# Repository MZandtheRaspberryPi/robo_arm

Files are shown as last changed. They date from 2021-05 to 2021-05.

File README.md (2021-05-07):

# robo_arm
This is a robot arm project that has two capabilities. The first is an arduino based arm that can be controlled via onboard joysticks and displays output to an OLED screen as it moves in x, y, z space with an inverse kinematic model. The second is a ROS Powered version that uses rosserial to communicate with the master node, and allows publishing of messages on a topic to command the arm in x, y, z coordinates.  
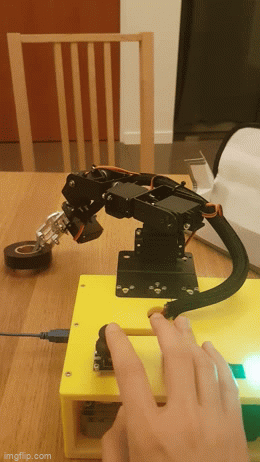
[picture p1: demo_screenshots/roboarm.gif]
roboarm
  

[Here](https://www.youtube.com/watch?v=9vvvBXWQKJA) is a demo of the arduino based version of the arm, and [here](https://www.youtube.com/watch?v=Fptv3H4Jj54) is a demo of the ros based version of the arm.  

The Arduino code for the ROS implementation is in the arduino_ros_arm folder, whereas the Arduino code for the standalone version is in the robo_arm_arduino_inverse_kinematics folder.

# Using the ROS Implementation
Follow the Steps in the Setting Up your Arm (ROS) section, and then launch the node:   
```
roslaunch robo_arm robo_arm.launch 
```  

And from here you can publish messages to control the arm:  
```
rostopic pub /robo_arm_teleop/arm_movement robo_arm/arm_control -1 '{x: 0, y: 180, z: 158, grip: 1700, duration: 1000}'
```  

# Table of Contents
[Project Phases](#Project-Phases)  
[Inverse Kinematics](#Inverse-Kinematics)  
[Setting Up your Arm (ROS)](#Setting-It-Up-ROS)  
[Setting Up your Arm (Arduino)](#Setting-It-Up-Arduino)   

# Project Phases
1. Repairing Arm
2. Testing Electronics
3. Initial Arduino Approach
4. 3d Modelling
5. Printing the Base
6. Assembly
7. Complex Arduino Software with IK Model
8. Complex ROS Software with IK Model

## Repairing the Arm
I actually got the raw parts for this arm from a friend, but it wasn't in working order when I got it, and didn't have any software.  It was too top heavy and the bottom servos couldn't support the weight well, and a lot of the joints weren't well secured. Also, the bottom piece of the arm had screws going into the plastic of the servo, so it couldn't rotate the arm left to right.    
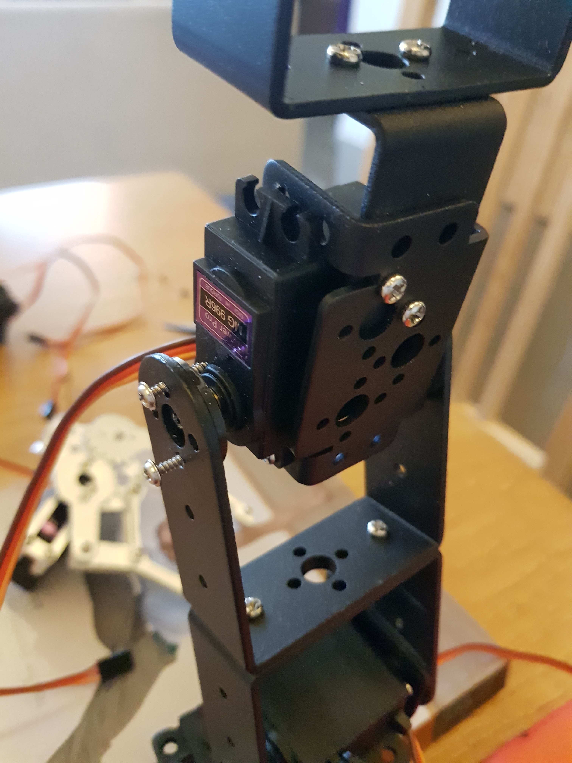
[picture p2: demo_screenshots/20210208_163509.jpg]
screws
   

I ended up replacing the servo horns with metal ones, that had screw holes that matched the screw holes of the metal body (M3). This helped me tighten the joints more securely, and not use long screws that could prevent rotation. I also removed a joint from the arm, bringing it from 6 to 5 joints to help it be not so top heavy.  

## Testing Electronics
From here, I rebuilt the arm and started testing the electronics system I wanted to put in place--powering the servos from Lipo Batteries through a 5v converter that can do up to 10 Amps.  
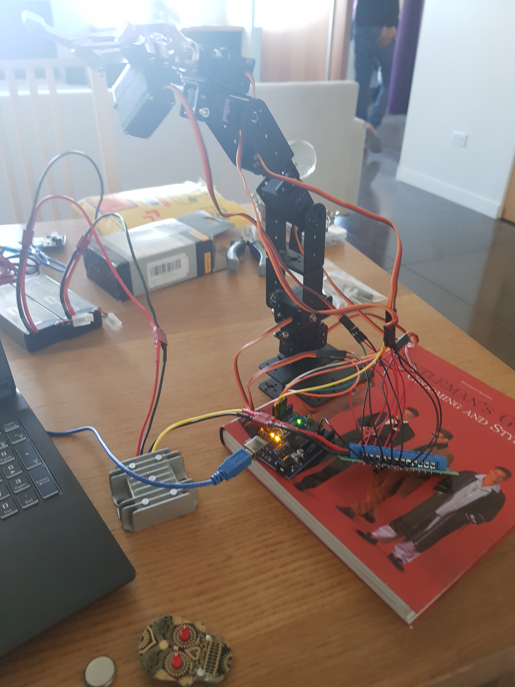
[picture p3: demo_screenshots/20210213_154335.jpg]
electronics
  

You can see here all the guts of the system with the emergency off switch, relay, OLED display, and more:  
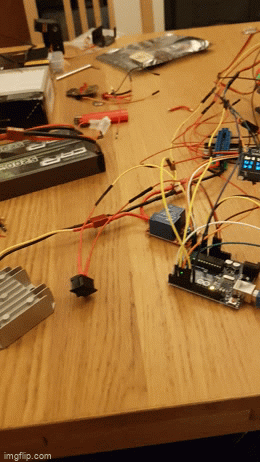
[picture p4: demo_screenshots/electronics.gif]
!electronics2
  

## Initial Arduino Approach
This would end up being simplistic code that moved each servo in angle space, moving them all in small steps to simulate coordinated motion. The Arduino code for this is in the robo_arm_arduino folder. It was an early prototype that I would build on in later software iterations, but it did serve as a proof of concept that coordinated movement was possible with the hardware setup. That said, if you wanted to move the gripper forward, you had to blend the angles yourself. Obviously this isn't ideal.  
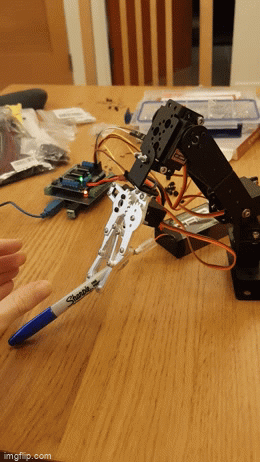
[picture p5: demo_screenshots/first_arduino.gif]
first_move
  

## 3d Modelling 
From here I wanted to tidy up the electronics, so I modelled a suitable base station. I first drew some sketches, picturing a base with electronics and the robo arm sitting on top.  
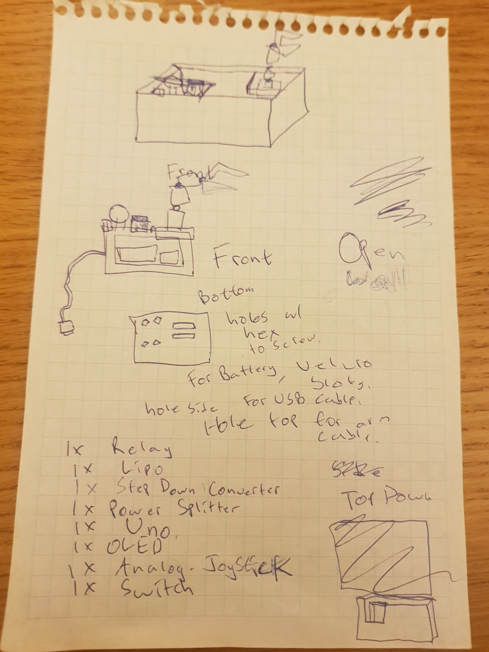
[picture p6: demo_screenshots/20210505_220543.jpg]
plan_for_model
  

And from here I modelled it in Fusion 360.
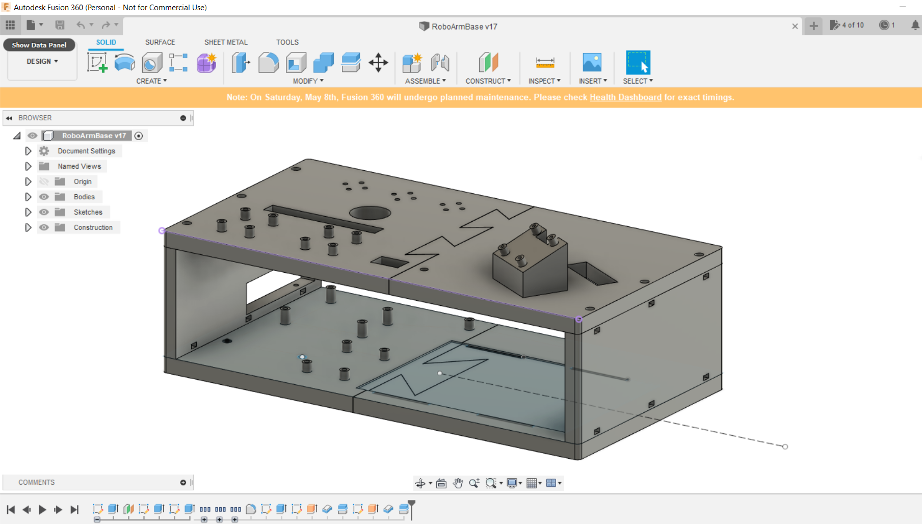
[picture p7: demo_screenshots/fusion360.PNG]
fusion360
  

Given this base was going to be quite big, 300mm by 155mm and 90mm tall, if I messed up any of the mounts or parts, it would take a lot to reprint it. So, I did a lot of prototyping for every single mounting point, as well as the mechanism that the sides of the base join to each other.  
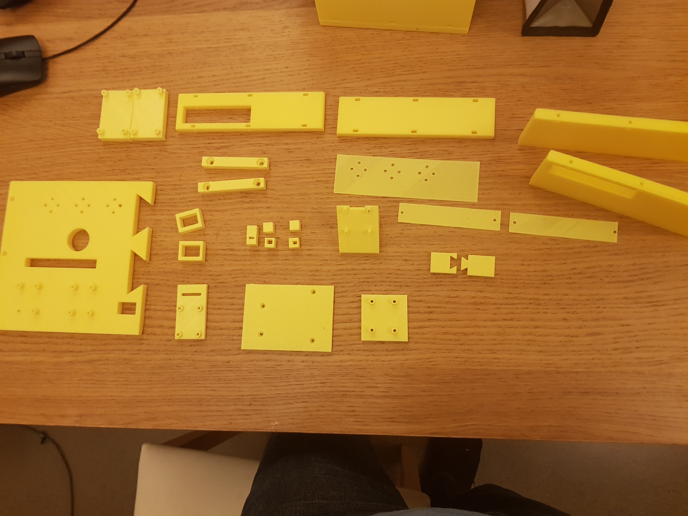
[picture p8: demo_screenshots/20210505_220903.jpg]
prototypes
  

## Printing the Base
I actually had some long put off maintenance that I had to do on my 3d printer. I put it off even longer, and kept having trouble getting prints to finish. For instance, look what I came home to one day:  
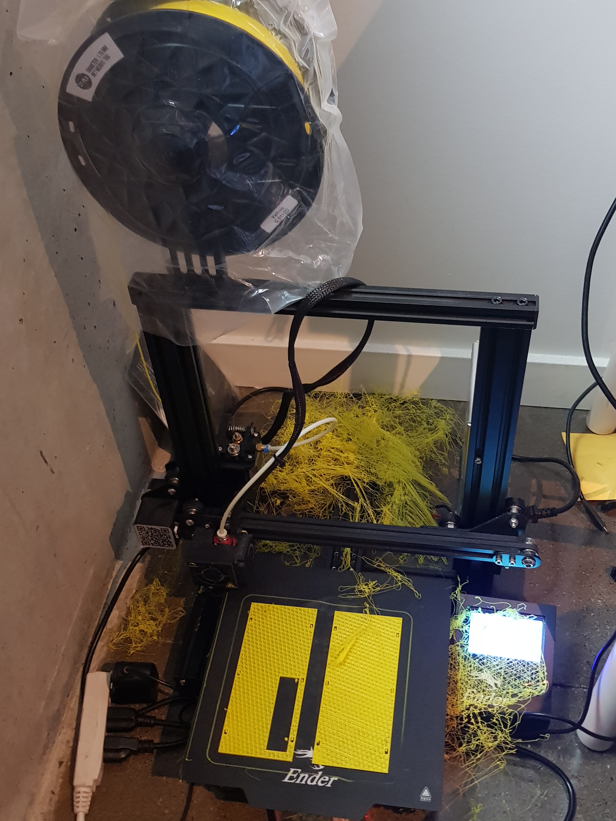
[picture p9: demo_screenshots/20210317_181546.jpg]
spaghetti
  

I eventually would install OctoPrint during this phase so that I could remotely monitor and shutdown my printer. I also replaced a clogged nozzle, replaced the springs on the 3d Printer Bed with stronger ones, and many other changes. Check out how gunked the nozzle was after one of the print failures:  
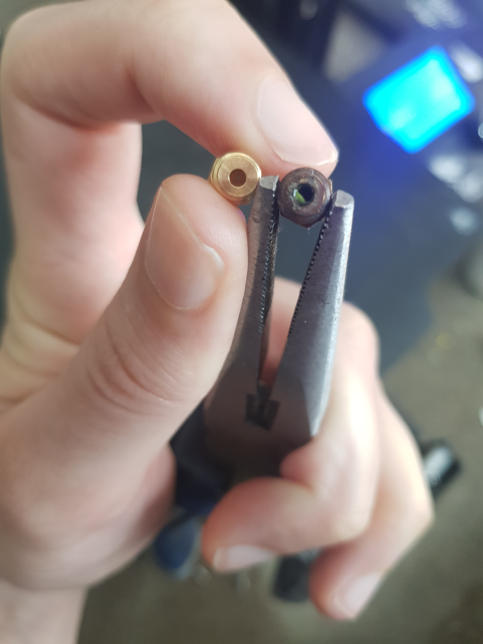
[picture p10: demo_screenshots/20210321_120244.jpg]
gunk
  

I also cleaned out the tube that feeds plastic to the extruder. you can see there was plastic stuck in it, which meant the extruder couldn't push the new plastic through:
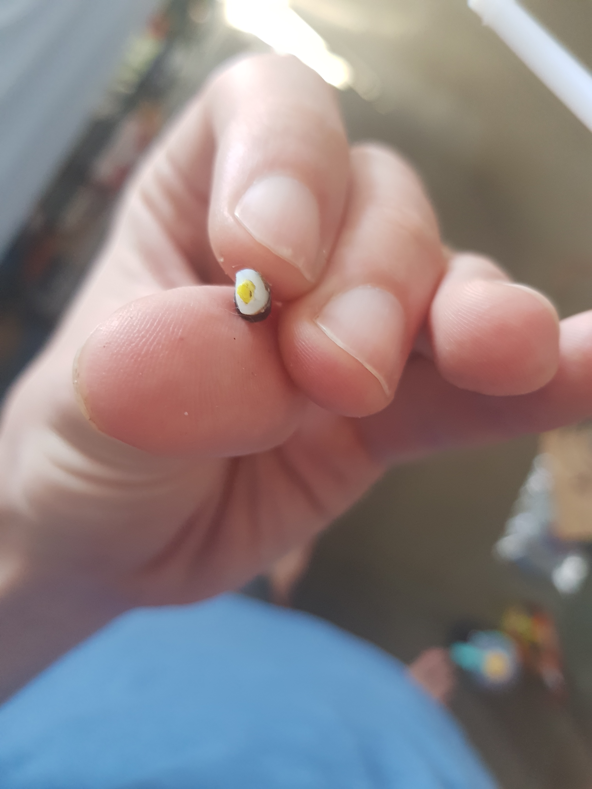
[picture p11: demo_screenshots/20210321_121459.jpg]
jam
  

This lead to problems where parts would be missing a layer, where the extruder got stuck and couldn't push plastic through:  
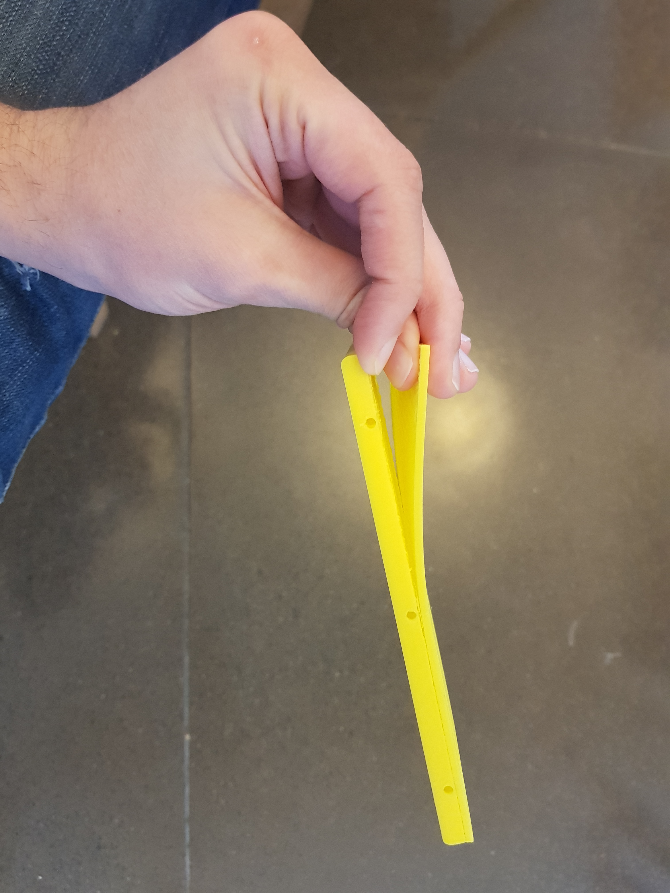
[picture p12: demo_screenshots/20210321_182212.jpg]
bad_ladyer
  

I also had an awkward problem, where when splitting up the top of the piece to print it in two seperate pieces (it was too big for my printer) I made a dovetail joint. That said, I split them using a 2mm surface instead of a .2mm surface and they couldn't fit back together again. Thankfully I only had to print one of these again as the surface extruded only into one side: 
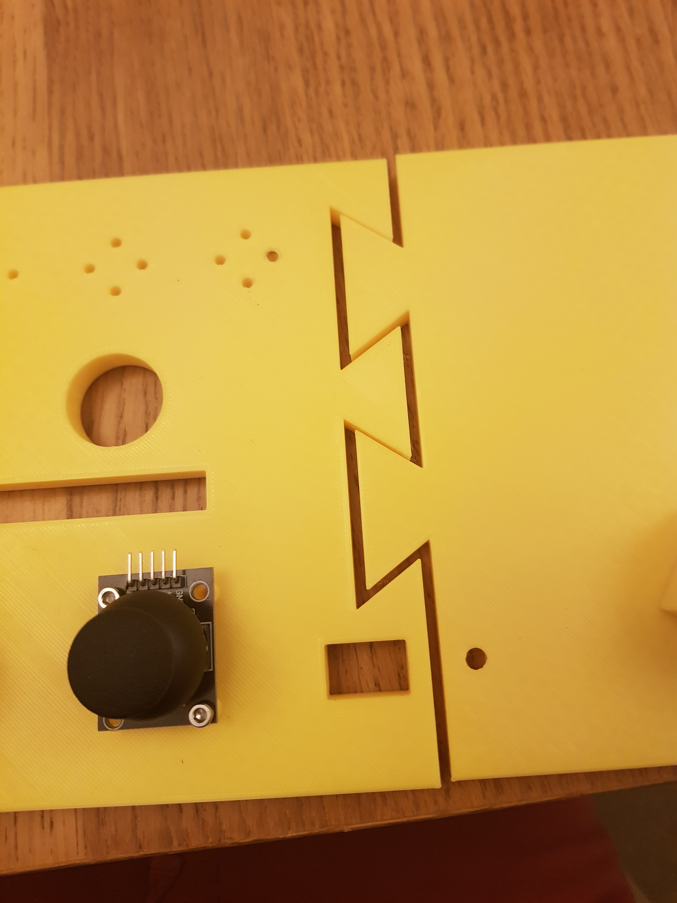
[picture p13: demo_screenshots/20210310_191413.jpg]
bad_extrude
  

I exited this phase having learned a lot about troubleshooting my printer, and having replaced a lot of parts to make the printer more durable and reliable in the future. Overall, a big win as I rely on this printer for many projects.  

## Assembly
Now I had my base and I started to assemble it with the electronics. You can see a sneak peek at everything and how it mounts. I still need to tidy up my wiring. In retrospect I could have designed wire channels into the base to help keep stuff tidy:  
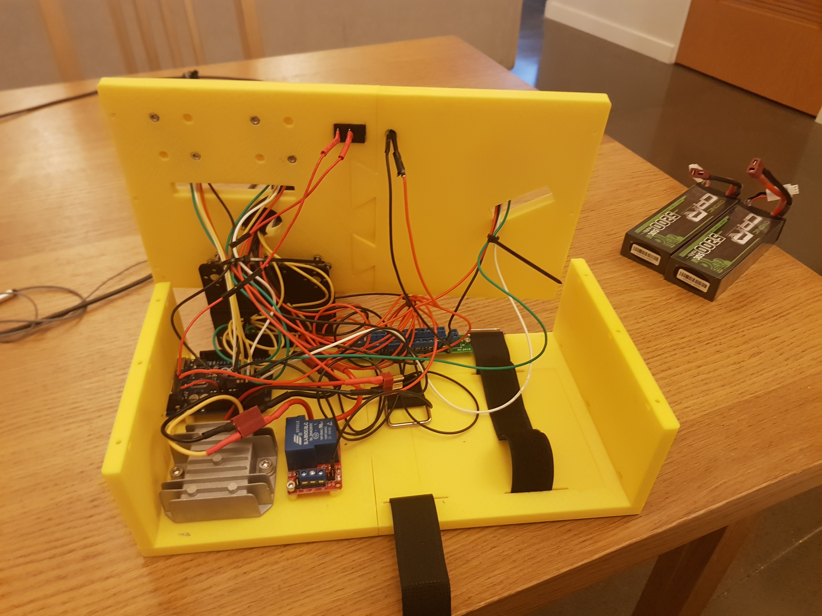
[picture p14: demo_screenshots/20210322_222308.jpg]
assembly
  

But from the top, it looks tidy:  
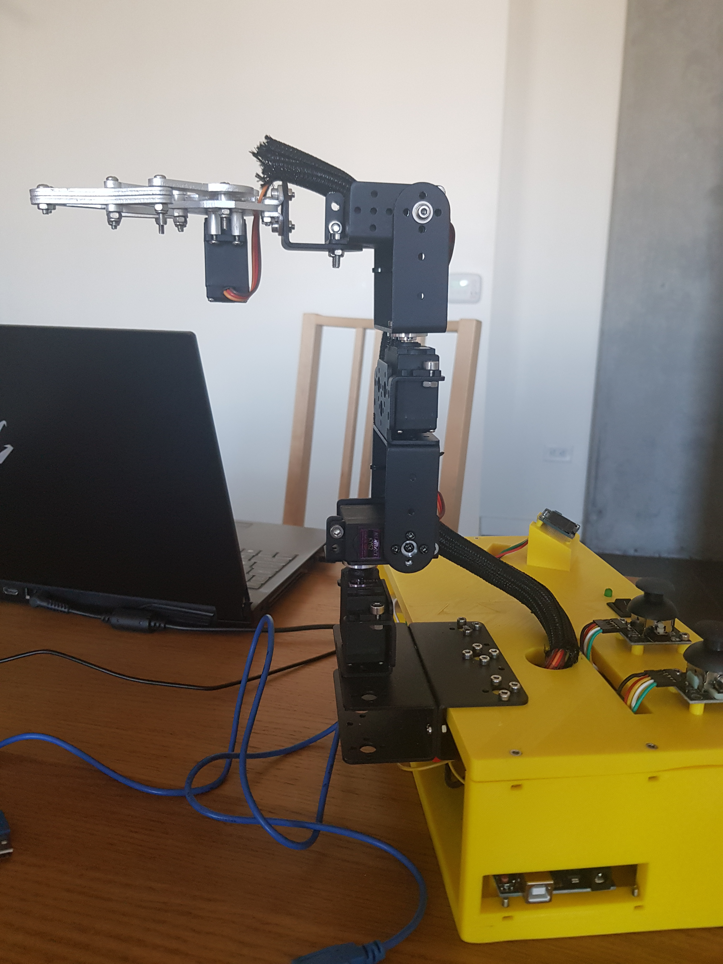
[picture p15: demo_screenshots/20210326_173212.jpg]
tidy
  

I did have a bit of a batery fiasco here where I left two batteries connected in serial for a couple nights. This lead to them overdischarging to probably about 2.5 volts, which is pretty bad. I ended up recharging them at a very low amperage, but these batteries are no longer safe to use or to charge, so I'm monitoring them carefully and will replace them soon.  

## Complex Arduino Software with IK Model
I ended up writing an IK model for the robot arm using some videos I saw from youtube and building on them to suit my robot. [This](https://www.youtube.com/watch?v=IN8tjTk8ExI)  video from James Bruton was very helpful. That said I had to make many changes for my IK model and develop some new functionality because my robot arm had different lengths for the upper and lower arm and because I added a third degree of freedom to my IK model as I wanted to control 3 servos, not 2. I'll talk about the kinematics after the project phases. That said, this software is available in the robo_arm_arduino_inverse_kinematics folder.  

## Complex ROS Software with IK Model
I started out writing pretty elaborate code to integrate the arm with ROS. I published a message with the joystick values from the robot, then on my laptop would publish a cmd_vel and a gripper control message off of that, but then when I started subscribing to those messages from the Arduino, I quickly ran out of space on the Arduino. The code for this is in the: ros_robo_arm_joy folder, and the ros code in the src folder as joy_listener.cpp. In my experience, one subscriber was already coming up close to the memory limits for the arduino, so I wanted to keep things simple. I settled on publishing a message from my laptop that had the x, y, z, gripper target, and how long to take to move there. From there the Arduino subscribed to that message and calculated the IKs to move the servos itself. The Arduino code for this approach that I settled on is in the arduino_ros_arm folder.

# Inverse Kinematics  
The IK model for this is pretty interesting. We take the point we command (x,y,z) as the point the gripper's jaws close on. Taking two dimensions, Z, X, we can solve for the arm length, and then use that to solve for various angles because we know all three sides of the ensueing triangle: 
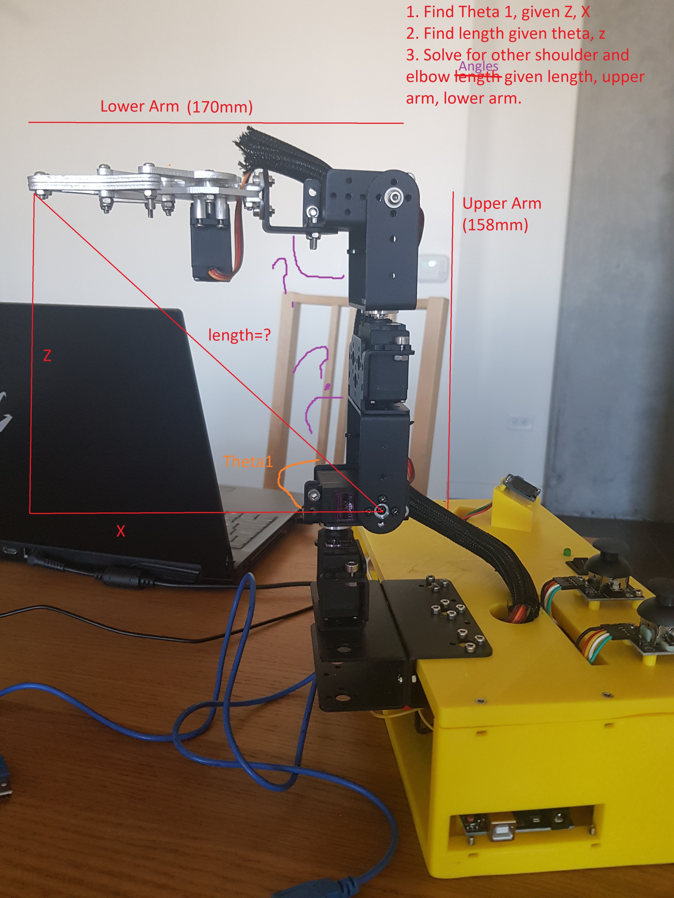
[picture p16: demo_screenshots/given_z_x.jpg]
ik
  

When we add in the third servo, the base servo of the arm, things get a tad more complicated.  

Consider this picture as if you were looking down at the robot arm and the base. Given x,y coordinates of the gripper, we can solve for the base servo angle of rotation. We can also solve for the length F that I've labeled that will be important in solving the rest of the angles.    
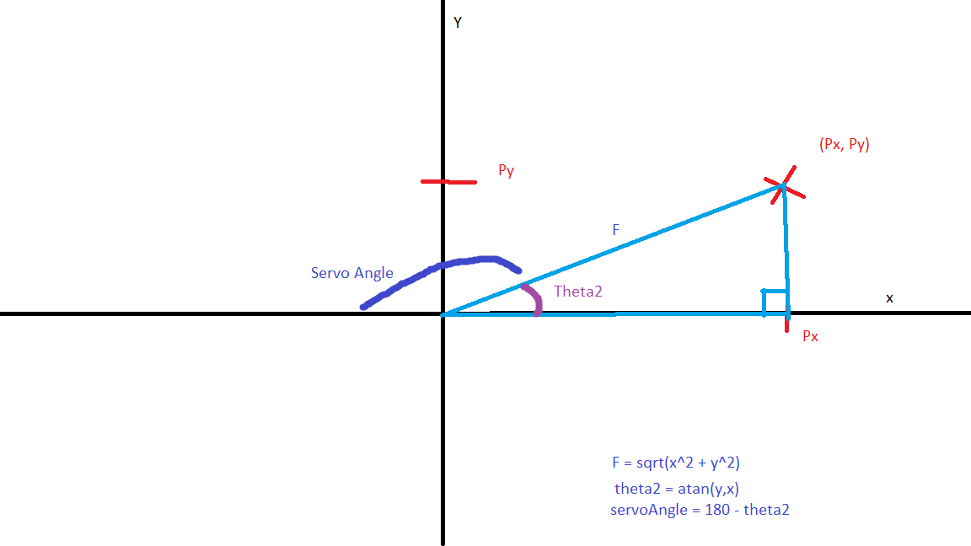
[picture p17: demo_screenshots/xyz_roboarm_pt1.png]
looking_down
  

Then in 3d space, we see F is the base of a triangle. We know the z coordinate, so can solve the third side of the triangle given its a right triangle. Now we have three sides of a triangle and we know the upper and lower arm lengths, so as per the first picture in this section we can solve the remaining two servos.
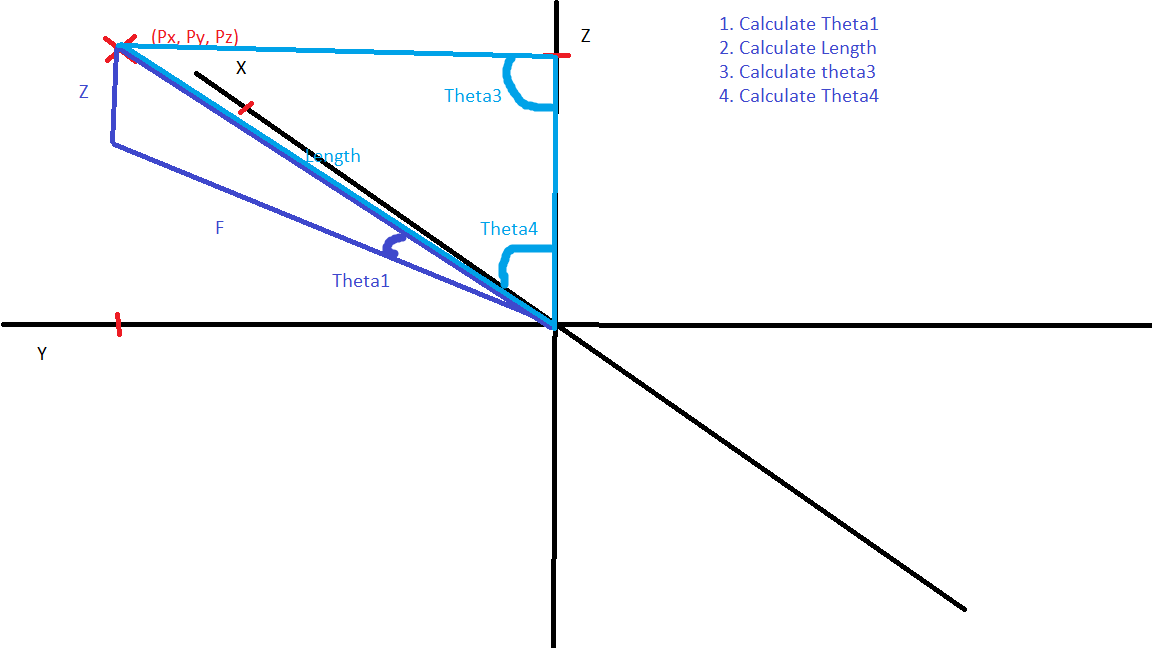
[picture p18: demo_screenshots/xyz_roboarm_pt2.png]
3d_space
  

You map everything together using offsets that come from how you've installed your servos. I didn't install mine so that when commanded to 45 degrees they made a 45 degree line with the table, so I had to have offsets for that.

# Setting It Up ROS

First, make a catkin workspace for the robo arm.
```
mkdir -p ~/robo_arm_catkin/src
cd ~/robo_arm_catkin/src
```

Then, clone the repo into the src folder of the catkin ws you created
```
git clone https://github.com/MZandtheRaspberryPi/robo_arm.git
```

Now you can make the catkin ws and then source it and run commands.
```
cd ~/robo_arm_catkin
catkin_make
source ~/robo_arm_catkin/devel/setup.bash
```

To generate the custom arduino messages, find the location of your arduino libraries folder and remove the ros_lib, and regenerate it. Make sure you've sourced the robo_arm workspace.
```
rm -rf /home/mz/Arduino/libraries/ros_lib
rosrun rosserial_arduino make_libraries.py ~/Arduino/libraries
```

Running the launch file. Note that my launch file that launches the serial node to communicate with the arm is set to ttyS0 as i'm using a VM and passing the com port to the VM. If you have your robo arm connected to a different serial port you'll need to edit the launch file and change the parameter for the serial port accordingly.
```
roslaunch robo_arm robo_arm.launch 
```

Early on, realized that having 1 publisher and 1 subscriber in an Arduino Uno was pushing memory limitations. Hence, trimmed down message with just changes in x, y, z, and gripper, and time to reach there.

message example:
```
rostopic pub /robo_arm_teleop/arm_movement robo_arm/arm_control -1 '{x: 0, y: 180, z: 158, grip: 1700, duration: 1000}'
```

# Setting It Up Arduino
The Arduino setup is more straightforward. Simply upload the code in the robo_arm_arduino_inverse_kinematics folder to the Arduino.

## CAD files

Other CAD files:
cad/RoboArmBase v17.f3d

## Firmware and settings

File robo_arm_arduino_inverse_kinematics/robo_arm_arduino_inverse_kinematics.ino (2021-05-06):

#include <Servo.h>
#include <SPI.h>
#include <Wire.h>
#include <Adafruit_GFX.h>
#include <Adafruit_SSD1306.h>
#include <Ramp.h>

#define SCREEN_WIDTH 128 // OLED display width, in pixels
#define SCREEN_HEIGHT 32

#define OLED_RESET     -1 // Reset pin # (or -1 if sharing Arduino reset pin)
#define SCREEN_ADDRESS 0x3C ///< See datasheet for Address; 0x3D for 128x64, 0x3C for 128x32
Adafruit_SSD1306 display(SCREEN_WIDTH, SCREEN_HEIGHT, &Wire, OLED_RESET);

unsigned long currentMillis;
unsigned long previousMillis;


class RoboArm {

  void showArmLength(int x, int y, int z, int baseAngle, int elbowAngle, int shoulderAngle){

    if (this->lastBaseAngle == baseAngle && this->lastElbowAngle == elbowAngle && this->lastShoulderAngle == shoulderAngle) {
      return;
    }
    
    display.clearDisplay();
    
    display.setCursor(0, 0);     // Start at top-left corner
    display.print("X: ");
    display.print(x);
    display.print(" Y: ");
    display.print(y);
    display.print(" Z: ");
    display.print(z);

    display.setCursor(0, 8);     // Start at top-left corner
    display.print("elbow: ");
    display.print(elbowAngle);

    display.setCursor(0, 16);     // Start at top-left corner
    display.print("shoulder: ");
    display.print(shoulderAngle);

    display.setCursor(0, 24);     // Start at top-left corner
    display.print("base: ");
    display.print(baseAngle);
    
    display.display();
    lastShoulderAngle = shoulderAngle;
    lastElbowAngle = elbowAngle;
    lastBaseAngle = baseAngle;
  }

    // init to setup up the servos
  public: 
  // some of hte setup stuff like attaching pins can only be done within the arduino setup function i suspect
  // i need to init this as a global variable, and so doing this in a seperate function instead of in constructor
  void setup(int basePin, int midPin, int upperPin, int gripperPin, int gripperRotationPin,
             int joystickLXPin, int joystickLYPin, int joystickLButtonPin,
             int joystickRXPin, int joystickRYPin, int joystickRButtonPin) {

      if(!display.begin(SSD1306_SWITCHCAPVCC, SCREEN_ADDRESS)) {
        Serial.println(F("SSD1306 allocation failed"));
        return;
      }
    
      display.clearDisplay();
      
      display.setCursor(0, 0);     // Start at top-left corner
      display.print("setting up arm");
      display.display();
      
      this->joystickLXPin = joystickLXPin;
      this->joystickLYPin = joystickLYPin;
      this->joystickLButtonPin = joystickLButtonPin;

      this->joystickRXPin = joystickRXPin;
      this->joystickRYPin = joystickRYPin;
      this->joystickRButtonPin = joystickRButtonPin;

      pinMode(joystickLYPin, INPUT);
      pinMode(joystickLXPin, INPUT);
      pinMode(joystickLButtonPin, INPUT_PULLUP);

      pinMode(joystickRXPin, INPUT);
      pinMode(joystickRYPin, INPUT);
      pinMode(joystickRButtonPin, INPUT_PULLUP);

      // attaching servos to pins
      baseServo.attach(basePin, baseServoLowerLimit, baseServoUpperLimit);
      shoulderServo.attach(midPin, shoulderLowerLimit, shoulderUpperLimit);
      elbowServo.attach(upperPin, elbowServoLowerLimit, elbowServoUpperLimit);
      gripperServo.attach(gripperPin, gripperServoLowerLimit, gripperServoUpperLimit);
      gripperRotationServo.attach(gripperRotationPin, gripperRotationServoLowerLimit, gripperRotationServoUpperLimit);
      delay(100);

      baseServo.writeMicroseconds(baseServoDefaultPos);
      shoulderServo.writeMicroseconds(shoulderDefaultPos);
      elbowServo.writeMicroseconds(elbowServoDefaultPos);
      gripperServo.writeMicroseconds(gripperServoClosedPos);
      gripperRotationServo.writeMicroseconds(gripperRotationServoDefaultPos);

  }

  float calculateElbowAngle(float upperLength, float lowerLength, float armLength){
      // C = arccos((a^2 + b^2 - c^2)/2ab)
      // elbowAngle = arccos((upperArm^2 + lowerArm^2 - armlength^2)/2*upperArm*lowerArm)
      // calculates in radians
      elbowAngleRadians = acos((sq(upperLength) + sq(lowerLength) - sq(armLength))/(2*upperLength*lowerLength));
      elbowAngleDegrees = elbowAngleRadians * (180/PI);
      return elbowAngleDegrees;
  }

  int elbowAngleToUs(float elbowAngleDegrees, int elbowOffsetUs){
      // firstly, get angles to us, then add in offset so that we have a us figure.
      // most servos have 11 ms per degree, so making into ms
      elbowAngleUs = (int) elbowAngleDegrees * 11;
      // we have an offset as 90 degrees, or 990us, isn't perpendicular to table in mine
//      elbowAngleUs += elbowOffsetUs;

      // as the degrees angle gets bigger, the microseconds need to decrease
      // because i've mounted my servo that way
      // to get to 110 degrees for example, the us has to decrease from what it was for 90.
      // so we find the change from default pos, and subtract it out from default pos
      // as calculated Us gets bigger, which will happen as angle gets bigger, we make final us smaller
//      elbowAngleUs = this->elbowServoDefaultPos - (elbowAngleUs - this->elbowServoDefaultPos);
      elbowAngleUs = this->elbowServoDefaultPos - (elbowAngleUs- 1000);
      return elbowAngleUs;
    
  }

  float calculateShoulderAngle(float upperLength, float lowerLength, float armLength){
      // B = arccos((a^2 + c^2 - b^2)/2*a*c)
      shoulderAngleRadians = acos((sq(upperLength) + sq(armLength) - sq(lowerLength))/(2*upperLength*armLength));
      shoulderAngleDegrees = shoulderAngleRadians * (180/PI);
      return shoulderAngleDegrees;
  }

  int shoulderAngleToUs(float shoulderAngleDegrees, int shoulderOffsetUs, float shoulderMs2){

      // most servos have 11 ms per degree, so making into ms
      shoulderAngleUs = (int) shoulderAngleDegrees * 11;
      // my servos aren't mounted so that the shoulder angle is 45degrees (in actuality 47 as my sides aren't equal of triangle
      // and it ain't isololes) when perpendicular to table, so adjust for that.
//      shoulderAngleUs += shoulderOffsetUs;

      // as the degrees angle gets bigger, the microseconds need to decrease
      // because i've mounted my servo that way
      // to get to 110 degrees for example, the us has to decrease from what it was for 90.
      // so we find the change from default pos, and subtract it out from default pos
      // as calculated Us gets bigger, which will happen as angle gets bigger, we make final us smaller
//      shoulderAngleUs = this->shoulderDefaultPos - (shoulderAngleUs - this->shoulderDefaultPos);
      shoulderAngleUs = this->shoulderDefaultPos - (shoulderAngleUs - 480) - shoulderMs2;
      return shoulderAngleUs;
  }

  int baseAngleToUs(float baseAngleDegrees){
    // map the degrees to the servo us of our base servo
    // when the base servo is like 700 us or so, it is pointing all the way to the right, 180 degrees
    // hence map bounds for us are flipped
    baseAngleUs = map(baseAngleDegrees, 0, 180, this->baseServoUpperLimit, this->baseServoLowerLimit);
    return baseAngleUs;
  }

  int readJoystickDirection(int pinToRead, int lowerMidCutoff, int upperMidCutoff, int lowerMap, int upperMap){
    xValue = analogRead(pinToRead);
    // often a bit of zone around middle joystick that you want to ignore to cut out noise
    if (xValue > upperMidCutoff || xValue < lowerMidCutoff) {
      xMap = map(xValue, 0, 1023, lowerMap, upperMap);
    }
    else {
      xMap = 0;
    }
    // our joysticks are placed on their side
    // so we get opposite values as we expect if we move joystick
    // moving x to the right should increase, moving y up should increase, so let's make it so
    xMap *= -1;
    return xMap;
  }

  bool readJoystickButton(int pinToRead, unsigned long lastButtonPress){
    SW_state = digitalRead(pinToRead);
    // make sure button can only be pressed once ever 400 ms or so
    if (SW_state == 0 && millis() - lastButtonPress > 400) {
      // button press increments selected servo, could resetting to 1 if we cycle through
      lastButtonPress = millis();
      return 1;
    }
    return 0;
  }

  void moveArm(float x, float y, float z, int gripperAngleUs){
    Serial.print("x: ");
    Serial.print(x);
    Serial.print(" y: ");
    Serial.print(y);
    Serial.print(" z: ");
    Serial.println(z);
    Serial.print("gripperAngleUs: ");
    Serial.println(gripperAngleUs);

    // solving for base servo angle first, given x and y
    float theta2 = atan2(y, x);
    float theta2Degrees = theta2 * (180/PI);
    float baseAngleDegrees = 180 - theta2Degrees;
    baseAngleUs = this->baseAngleToUs(baseAngleDegrees);
    Serial.print("baseAngleDegrees: ");
    Serial.print(baseAngleDegrees);
    Serial.print(" baseAngleUs: ");
    Serial.println(baseAngleUs);

    // distance to x,y,z point in just x and y space
    float f = sqrt(sq(x) + sq(y));
    Serial.print("f: ");
    Serial.println(f);

    // given f and z, we calculate theta 1 angle
    float theta1 = atan2(z, f);
    // given theta 1 and Z, we calculate the arm length
    // cos(theta1) = adj/hypotenuse
    this->armLength = (float)f / cos(theta1);
    
    float shoulderAngle2a = theta1 - 0.7853908;  // take away the default 45' offset (in radians)
    float shoulderAngle2aDegrees = shoulderAngle2a * (180/PI);    // degrees
    float shoulderMs2 = shoulderAngle2aDegrees * 11;

    elbowAngleDegrees = this->calculateElbowAngle(upperLength, lowerLength, armLength);
    Serial.print("elbowAngleDegrees: ");
    Serial.print(elbowAngleDegrees);
    elbowAngleUs = this->elbowAngleToUs(elbowAngleDegrees, elbowOffsetUs);
    Serial.print(" elbowAngleUs: ");
    Serial.println(elbowAngleUs);
    shoulderAngleDegrees = this->calculateShoulderAngle(upperLength, lowerLength, armLength);
    Serial.print("shoulderAngleDegrees: ");
    Serial.print(shoulderAngleDegrees);
    shoulderAngleUs = this->shoulderAngleToUs(shoulderAngleDegrees, shoulderOffsetUs, shoulderMs2);
    Serial.print(" shoulderAngleUs: ");
    Serial.println(shoulderAngleUs);
    this->showArmLength(x, y, z, baseAngleUs, elbowAngleUs, shoulderAngleUs);
    Serial.println();
    
    elbowServo.writeMicroseconds(elbowAngleUs);
    shoulderServo.writeMicroseconds(shoulderAngleUs);
    baseServo.writeMicroseconds(baseAngleUs);
    gripperServo.writeMicroseconds(gripperAngleUs);
    
  }

  public:
  void robotLoop(){
    
    changeXPos = readJoystickDirection(this->joystickLXPin,  425, 600, -3, 3);
    changeYPos = readJoystickDirection(this->joystickLYPin,  425, 600, -3, 3);
    if (readJoystickButton(this->joystickLButtonPin, this->lastLButtonPress)){
      Serial.println("L Button Pressed");
    }

    changeGripperPos = readJoystickDirection(this->joystickRXPin,  425, 600, -8, 8);
    changeZPos = readJoystickDirection(this->joystickRYPin,  425, 600, -3, 3);
    if (readJoystickButton(this->joystickRButtonPin, this->lastRButtonPress)){
      Serial.println("R Button Pressed");
    }

    x += changeXPos;
    y += changeYPos;
    z += changeZPos;

    if (gripperAngleUs + changeGripperPos > gripperServoLowerLimit && gripperAngleUs + changeGripperPos < gripperServoUpperLimit) {
      gripperAngleUs += changeGripperPos;
    }

    this->moveArm(x, y, z, gripperAngleUs);
  }

private:
  // defaults in microseconds
  Servo baseServo;
  // default is 90 degrees
  // 1500 microseconds
  int baseServoDefaultPos = 1530;
  // this is gripper pointing to right of base
  int baseServoLowerLimit = 690;
  // this is gripper pointing to left of base
  int baseServoUpperLimit = 2300;
  Servo shoulderServo;
  // 780 is about straight up and down, ie, 90 degrees with table
  // as Ms gets smaller, arm moves towards joysticks
  int shoulderDefaultPos = 800;
  int shoulderLowerLimit = 650;
  // 100 degrees
  int shoulderUpperLimit = 1500;
  // 45 degrees at 11us per degree is 495us
  // my shoulder is at 45 degree position when us is 780
  // therefore, add an offset of 800 - 495 to the calculated shoulderUs
  int shoulderOffsetUs = shoulderDefaultPos - 495;
  Servo elbowServo;
  // 1730 is about parallel to the table
  // elbow servo mounted so that as microseconds decrease, it rotates away from robo arm base (ie, upward)
  int elbowServoDefaultPos = 1730;
  int elbowServoLowerLimit = 790;
  int elbowServoUpperLimit = 2210;
  // 90 degrees at 11us per degree is 990us
  // my elbow is at 90 degree position when us is 1730
  // therefor, add an offset of 1730-990 to the calculated eblowUs
  int elbowOffsetUs = 1730 - 990;
  Servo gripperServo;
  // 1640 is open
  // 2080 is closed about
  int gripperServoOpenPos = 1640;
  int gripperServoClosedPos = 2080;
  int gripperServoDefaultPos = gripperServoOpenPos;
  int gripperServoLowerLimit = 1490;
  int gripperServoUpperLimit = 2200;
  Servo gripperRotationServo;
  // 
  int gripperRotationServoDefaultPos = 1220;
  int gripperRotationServoLowerLimit = 700;
  int gripperRotationServoUpperLimit = 1890;

  int selectedServo = 1;
  int joystickLXPin;
  int joystickLYPin;
  int joystickLButtonPin;

  int joystickRXPin;
  int joystickRYPin;
  int joystickRButtonPin;
  
  unsigned long lastLButtonPress;
  unsigned long lastRButtonPress;

  int xValue;
  int yValue;
  int xMap;
  int yMap;
  int SW_state;

  int changeXPos;
  int changeYPos;
  int changeZPos;
  int changeGripperPos;

  // c^2 = a^2 + b^2 -2abCos(C)
  // lower is the arm between gripper and upper mid servo
  float lowerLength = 170;
  // upper is the arm between mid servo and upper mid servo
  float upperLength = 158;
  
  float elbowAngleDegrees;
  float elbowAngleRadians;
  float shoulderAngleDegrees;
  float shoulderAngleRadians;

  int elbowAngleUs;
  int shoulderAngleUs;
  int baseAngleUs;
  int gripperAngleUs = gripperServoDefaultPos;
  
  // armLength is from mid servo to tip of gripper servo
  // we'll set this at the start and use it to solve for the angles in the upper arm
  // 233 is about the hypotenuse that sets shoulder to 90 degrees and elbow to 45 degrees, ie upper arm perpendicular to table
  float armLength = 233;

  // elbow offset is because I didn't mount the servo so that when I commanded it to 90 it would be
  // perpendicular to the table. I mounted it so that when it is at 122 it is perpendicular to the table.
  int elbowOffset = 122-90;
  // similar with shoulder offset
  int shoulderOffset = 18-47;


  // this is for display, so we don't have to update each loop if hasn't changed:
  int lastBaseAngle;
  int lastElbowAngle;
  int lastShoulderAngle;


  // setting x, y, z coords in mm
  float x = 0;
  float y = 170;
  float z = 158;
};

RoboArm mz_robot;

void setup() {
  Serial.begin(57600);
  Serial.println("Starting setup");
  display.setTextSize(1);      // Normal 1:1 pixel scale
  display.setTextColor(SSD1306_WHITE); // Draw white text
  // basePin, int midPin, int upperPin, int gripperPin, int gripperRotationPin
  mz_robot.setup(4, 5, 7, 8, 6, A0, A1, 2, A2, A3, 3);
  delay(2000);
  Serial.println("Done with setup");
  display.clearDisplay();
}

void loop() {
  currentMillis = millis();

  if (currentMillis - previousMillis >= 10) {  // start timed loop
      previousMillis = currentMillis;
      mz_robot.robotLoop(); 
  }
  
}

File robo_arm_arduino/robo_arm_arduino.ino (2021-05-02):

#include <Servo.h>
#include <SPI.h>
#include <Wire.h>
#include <Adafruit_GFX.h>
#include <Adafruit_SSD1306.h>

#define SCREEN_WIDTH 128 // OLED display width, in pixels
#define SCREEN_HEIGHT 32

#define OLED_RESET     -1 // Reset pin # (or -1 if sharing Arduino reset pin)
#define SCREEN_ADDRESS 0x3C ///< See datasheet for Address; 0x3D for 128x64, 0x3C for 128x32
Adafruit_SSD1306 display(SCREEN_WIDTH, SCREEN_HEIGHT, &Wire, OLED_RESET);

// current values
//int joystickLXPin = A0;
//int joystickLYPin = A1;
//int joystickLButtonPin = 2;
//
//int joystickRYPin = A3;
//int joystickRXPin = A2;
//int joystickRButtonPin = 3;

//pinMode(joystickLButtonPin, INPUT_PULLUP);
//pinMode(joystickRButtonPin, INPUT_PULLUP);

//Servo baseServo;
//Servo midServo;
//Servo upperServo;
//Servo gripperServo;
//Servo gripperRotationServo;

// Robot Joint Motion Stuctures
struct armPos {
  int baseServoAngle;
  int midServoAngle ;
  int upperServoAngle ;
  int gripperServoAngle;
  int gripperRotationAngle;
  int desiredDelay ;
};

struct armPos armMotion;  // Joint Positions of arm


class RoboArm {
  // init to setup up the servos
  public: 
  // some of hte setup stuff like attaching pins can only be done within the arduino setup function i suspect
  // i need to init this as a global variable, and so doing this in a seperate function instead of in constructor
  void setup(int basePin, int midPin, int upperPin, int gripperPin, int gripperRotationPin,
             int joystickXPin, int joystickYPin, int joystickButtonPin) {
      this->joystickXPin = joystickXPin;
      this->joystickYPin = joystickYPin;
      this->joystickButtonPin = joystickButtonPin;

      pinMode(joystickYPin, INPUT);
      pinMode(joystickXPin, INPUT);
      pinMode(joystickButtonPin, INPUT_PULLUP); 
      
      // attaching servos to pins
      baseServo.attach(basePin);
      midServo.attach(midPin);
      upperServo.attach(upperPin);
      gripperServo.attach(gripperPin);
      gripperRotationServo.attach(gripperRotationPin);
      delay(500);   
  }

  int servoParallelControl (int thePos, Servo theServo, int theSpeed ) {
      // this is a function to move a single servo by a small amount each time
      // and return whether we reach the final position
      // it is designed to be called many timeas to get to one position, by the function moveTo
      Serial.println("moving servo");

      int startPos = theServo.read();        //read the current pos
      int newPos = startPos;
      Serial.print(startPos);
      Serial.print(" ");
      Serial.println(newPos);
    
      //define where the pos is with respect to the command
      // if the current position is less that the actual move up
      if (startPos < (thePos - 5)) {
        newPos = newPos + 1;
        theServo.write(newPos);
        delay(theSpeed);
        return 0;
      }

      // else move the servo down
      else if (newPos > (thePos + 5)) {
        newPos = newPos - 1;
        theServo.write(newPos);
        delay(theSpeed);
        return 0;
      }

      // else we are at the desired position, or within 5 degrees
      else {
        return 1;
      }
   }

  void updateDisplay() {
    
    if(!display.begin(SSD1306_SWITCHCAPVCC, SCREEN_ADDRESS)) {
      Serial.println(F("SSD1306 allocation failed"));
      return;
    }
    
    display.clearDisplay();
    

    int servoPos;
    servoPos = baseServo.read();
    display.setCursor(0, 0);     // Start at top-left corner
    display.print("Base: ");
    display.print(servoPos);

    servoPos = midServo.read();
    display.setCursor(0, 10);     // Start at top-left corner
    display.print("Mid: ");
    display.print(servoPos);

    servoPos = upperServo.read();
    display.setCursor(0, 20);     // Start at top-left corner
    display.print("Up: ");
    display.print(servoPos);

    servoPos = gripperServo.read();
    display.setCursor(65, 0);     // Start at top-left corner
    display.print("Grip: ");
    display.print(servoPos);

    servoPos = gripperRotationServo.read();
    display.setCursor(65, 10);
    display.print("Gr Rot: ");
    display.print(servoPos);

    display.setCursor(65, 20);
    display.print("Sel: ");
    display.print(selectedServo);
  
    display.display();
  }



  public: 
  void moveTo(struct armPos armMotion) {
  
    int status1 = 0;
    int status2 = 0;
    int status3 = 0;
    int status4 = 0;
    int status5 = 0;
    int done = 0 ;
  
    while ( done == 0) {
      //move all servos to the desired position
      //this loop will cycle through the servos sending each the desired position.
      //Each call will cause the servo to iterate about 1-5 degrees
      //the rapid cycle of the loop makes the servos appear to move simultaneously
      status1 = servoParallelControl(armMotion.baseServoAngle, baseServo, armMotion.desiredDelay);
      status2 = servoParallelControl(armMotion.midServoAngle, midServo, armMotion.desiredDelay);
      status3 = servoParallelControl(armMotion.upperServoAngle, upperServo, armMotion.desiredDelay);
      status4 = servoParallelControl(armMotion.gripperServoAngle, gripperServo, armMotion.desiredDelay);
      status5 = servoParallelControl(armMotion.gripperRotationAngle, gripperRotationServo, armMotion.desiredDelay);
  
      //continue until all have reached the desired position
      if (status1 == 1 & status2 == 1 & status3 == 1 & status4 == 1 & status5 == 1) {
        done = 1;
        updateDisplay();
      }
    }// end of while
  } //function end

  public:
  void listenJoystick(){
    int xValue;
    int yValue;
    int xMap;
    int yMap;
    int SW_state;

    SW_state = digitalRead(joystickButtonPin);
    xValue = analogRead(joystickXPin);
    yValue = analogRead(joystickYPin);
    if (xValue > 535 || xValue < 488) {
      xMap = map(xValue, 0, 1023, -1, 1);
    }
    else {
      xMap = 0;
    }

    if (yValue > 535 || yValue < 488) {
      yMap = map(yValue, 0, 1023, -1, 1);
    }
    else {
      yMap = 0;
    }

    // make sure button can only be pressed once ever 400 ms or so
    if (SW_state == 0 && millis() - lastButtonPress > 400) {
      // button press increments selected servo, resetting to 1 if we cycle through
      selectedServo += 1;
      if (selectedServo > 5) {
        selectedServo = 1;
      }
      lastButtonPress = millis();
      updateDisplay();
    }
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

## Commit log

2021-02-09 Create servo_test
2021-02-15 adding arduino code for robo arm arduino version
2021-05-02 putting inverse kinematics into repo
2021-05-06 updating both ros and arduino robo_arm
2021-05-07 adding cad
    [RoboArmBase v17.f3d]
